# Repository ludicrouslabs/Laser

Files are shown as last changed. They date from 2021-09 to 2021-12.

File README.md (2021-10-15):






## Overview

This all came about due to a need to cut bulk acrylic for some friends and getting sick and tired of loading a CNC router to do it. And I’d be remiss if I didn’t admit this all wouldn’t have happened if a major manufacturer of laser engravers would have simply returned our calls.

With the accessibility of 3D printing and the ability to buy off the shelf components to make almost any machine you can think of, we figured a high-speed engraving laser couldn’t be that hard…. Or could it? Our goal is to make a safe, aesthetically pleasing laser platform that will enable makers to start with mostly 3d printed parts, while giving those who want a more professional system to upgrade to higher quality components. 

Lets see how close this gets.



## Design Status

| Assembly | Progress | Status | Comments | 
|---|:---:|---|---|
| Frame |  | Beta | Build at own risk |
| Panels |  | Beta | Build at own risk |
| X Drive |  | Design | Do not build / Errors expected |
| Y Drive |  | Beta | Build at own risk |
| Z Drive |  | Design | Do not build / Errors expected |
| Z Table |  | Design | Do not build / Errors expected |
| Laser Head |  | Design | Do not build / Errors expected |
| Electrical |  | Design | Do not build / Errors expected |
| Branding |  | Complete | Sticker design complete |

## Documentation

Documentation will become available when the initial design is tested and shown to work as expected.

## Getting Help
discord (https://discord.gg/RAaGxKcNBF)

## Shout Outs

Special thanks to RCF, Steve, Chron, Wile and everyone else for answering the endless stupid questions.

## Licence

All Ludicrous Labs projects are licenced GPL3.

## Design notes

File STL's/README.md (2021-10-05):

# STL's

Please be aware that this project is still in heavy development. None of the STL's should be considered complete or ready for and end user to build. Files posted here are intended for specific testers to download components for reference and review.

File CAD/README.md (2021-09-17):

# CAD

To be uploaded upon completion of initial design.

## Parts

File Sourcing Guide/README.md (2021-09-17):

# Sourcing Guide

Google sheet to be linked at a later date. Much to work on.

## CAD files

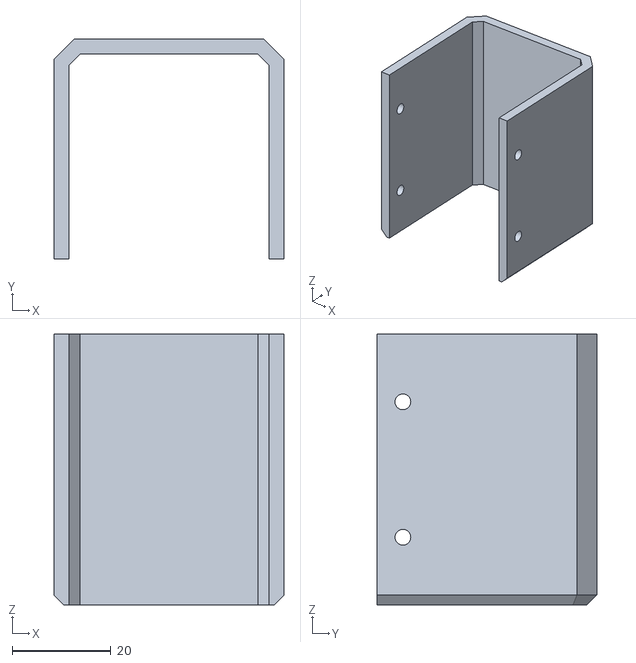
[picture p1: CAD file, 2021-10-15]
STL's/Head/head cover.stl
46.6 x 44.6 x 55.0

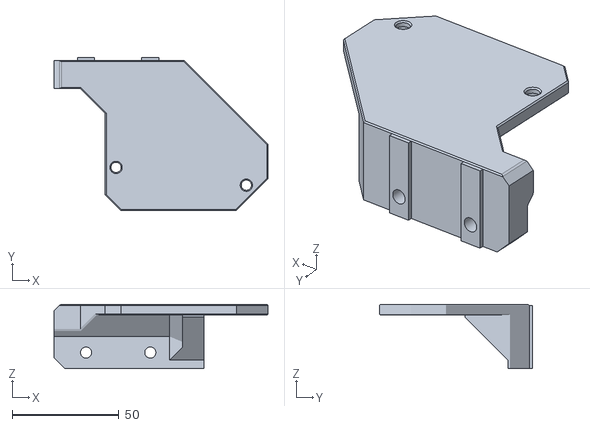
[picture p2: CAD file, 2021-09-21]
STL's/Tools/Test Platform.stl
100.0 x 71.5 x 30.0

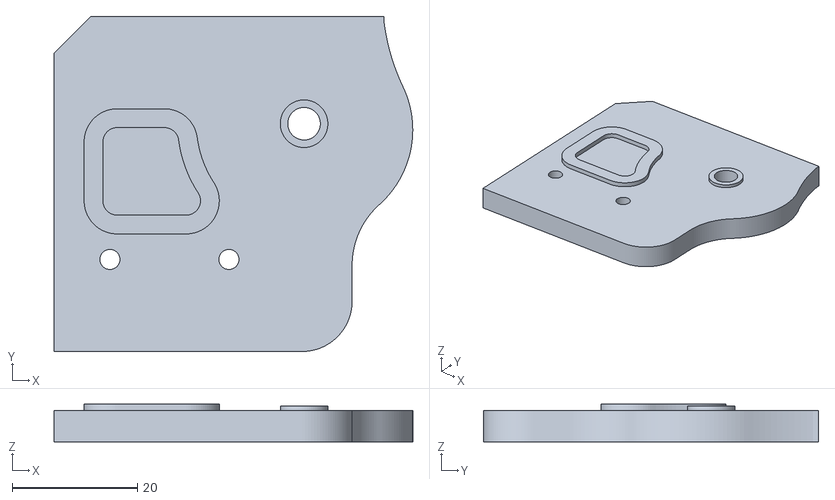
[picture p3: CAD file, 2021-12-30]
STL's/X Drive/X Drive Shim.stl
57.3 x 53.5 x 6.00

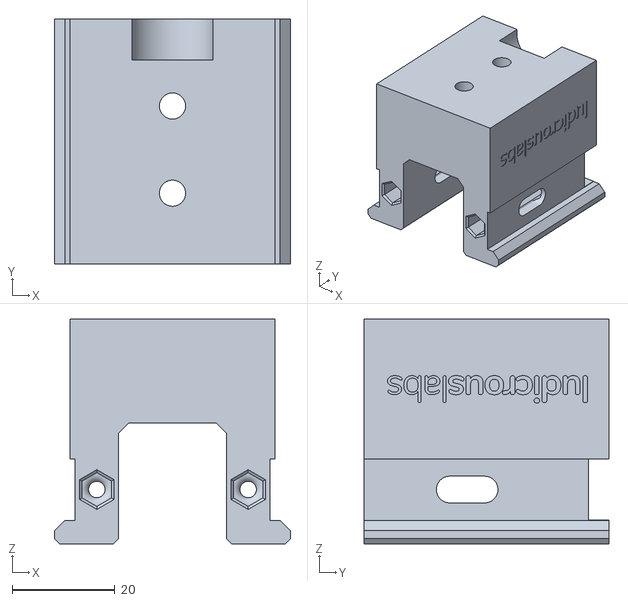
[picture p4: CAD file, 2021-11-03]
STL's/Y Drive/Y Block Top Right.stl
46.0 x 47.8 x 43.8

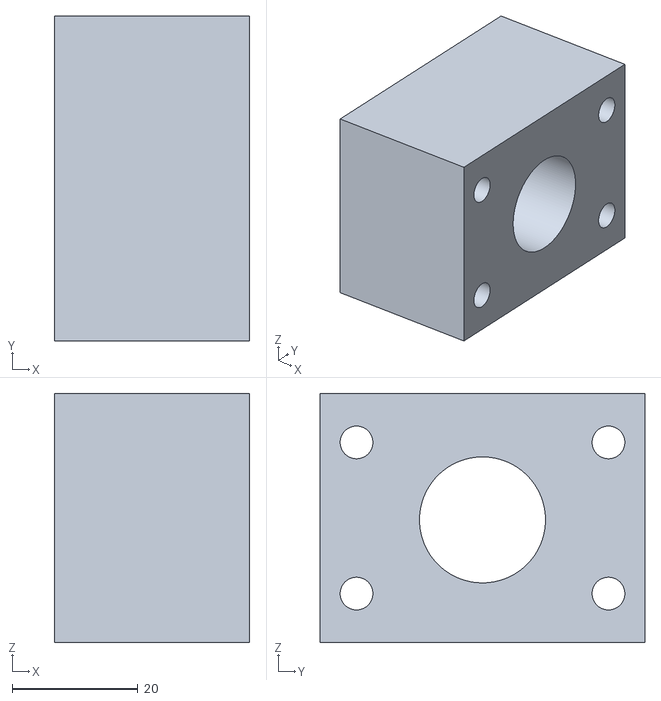
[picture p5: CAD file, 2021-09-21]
STL's/Z Drive/Bed Mount.stl
31.0 x 51.6 x 39.6

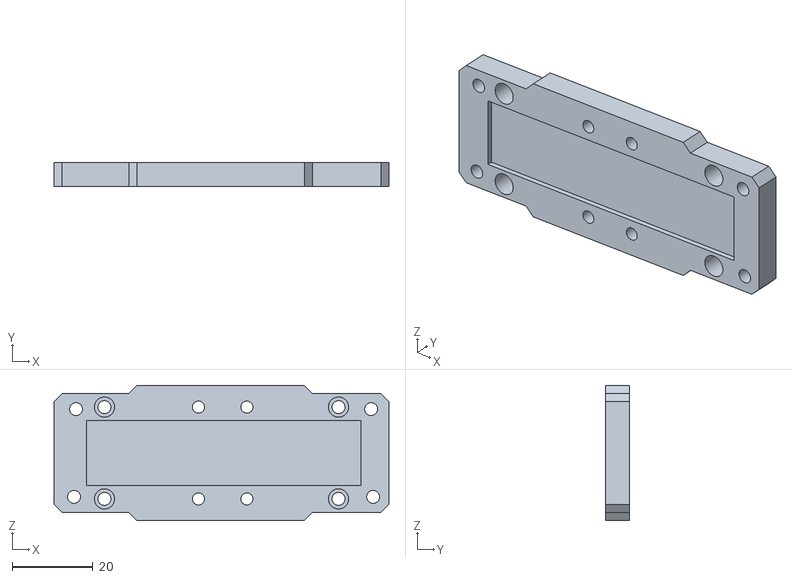
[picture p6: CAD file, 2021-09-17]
STL's/Head/face block.stl
83.0 x 6.00 x 33.5

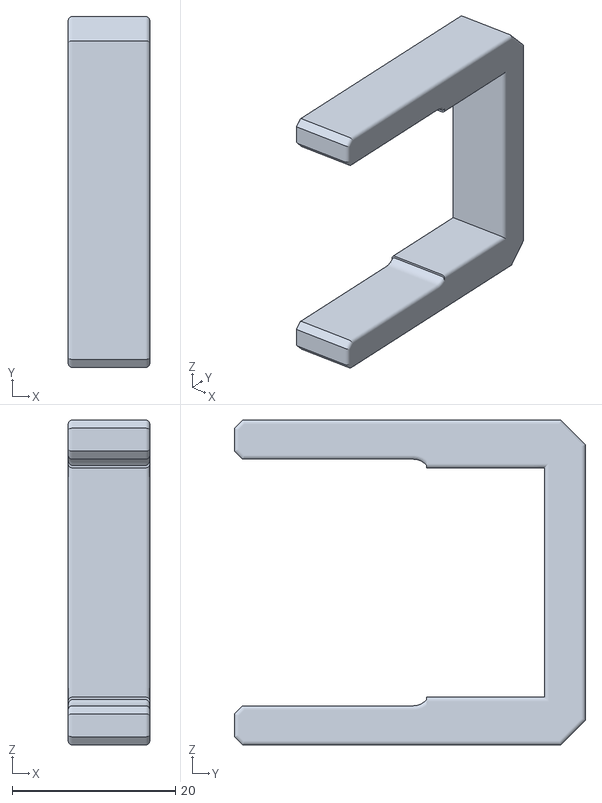
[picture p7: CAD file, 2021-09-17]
STL's/Tools/Alignment Guide.stl
10.0 x 43.0 x 39.8

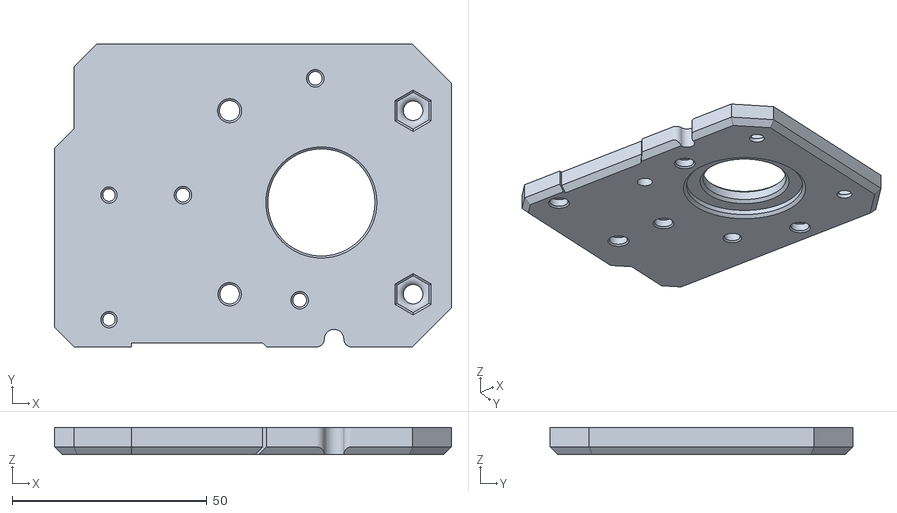
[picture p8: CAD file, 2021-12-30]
STL's/X Drive/X Drive Top.stl
102.0 x 77.8 x 7.00

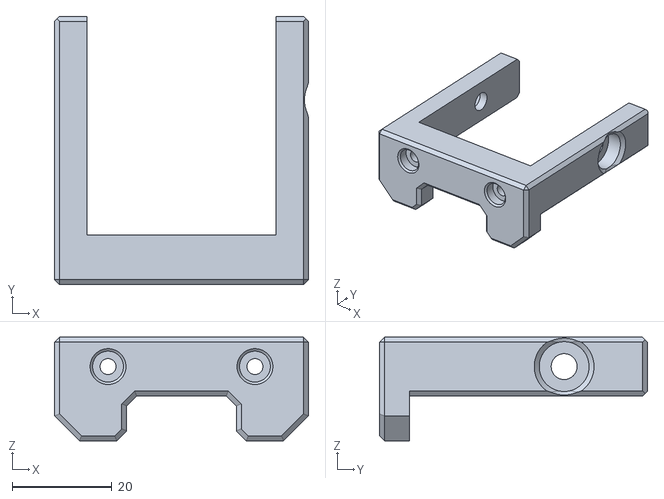
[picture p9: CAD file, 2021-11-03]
STL's/Y Drive/Tension Bracket Right.stl
51.0 x 53.8 x 20.8

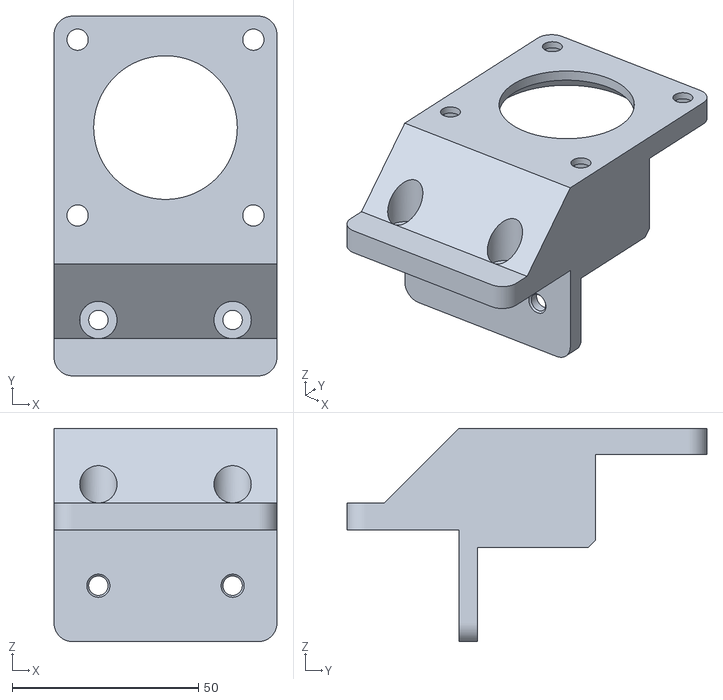
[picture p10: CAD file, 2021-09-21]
STL's/Z Drive/Z Motor Mount Right.stl
59.8 x 96.5 x 57.2

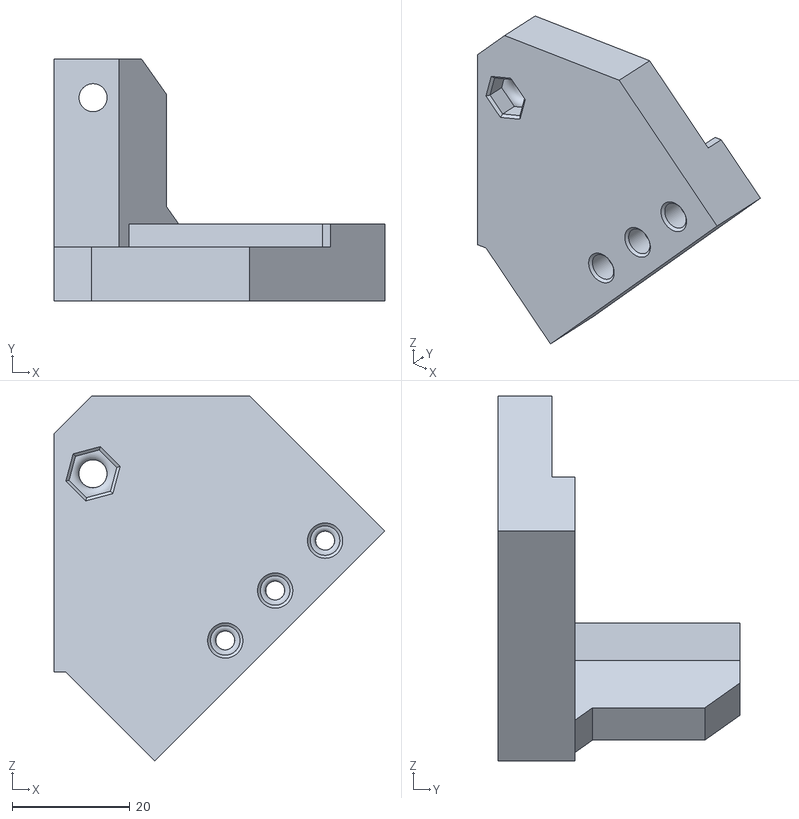
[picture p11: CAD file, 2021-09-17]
STL's/Head/mirror mount.stl
56.2 x 41.2 x 62.0

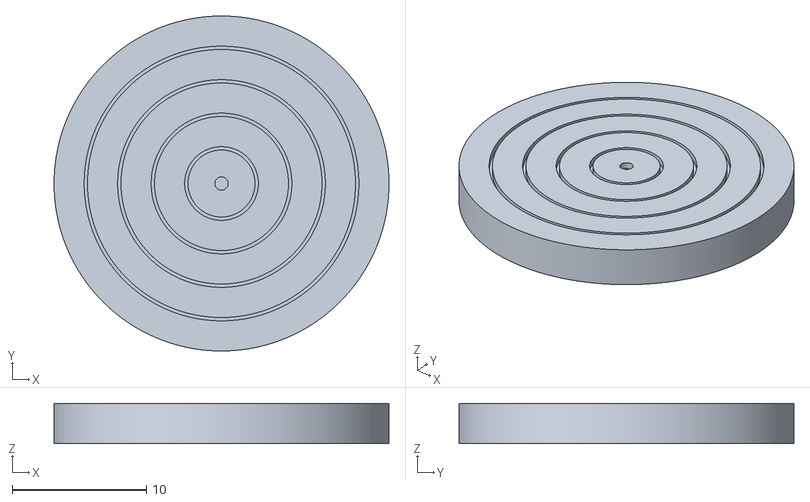
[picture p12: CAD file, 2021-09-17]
STL's/Tools/Target.stl
25.0 x 25.0 x 3.00

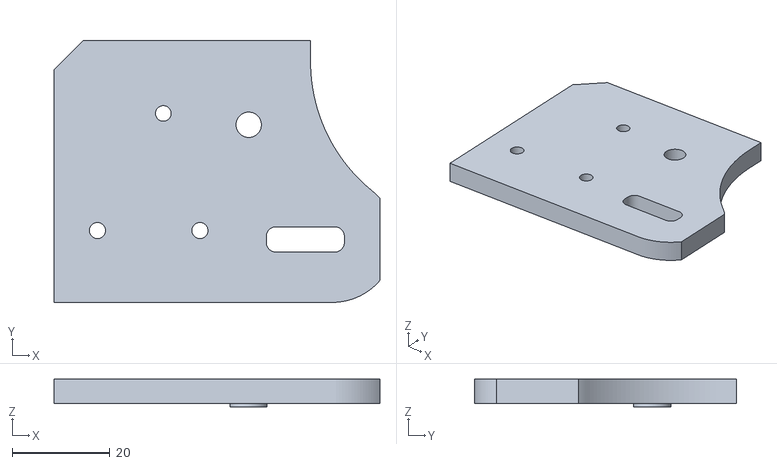
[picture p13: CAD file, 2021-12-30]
STL's/X Drive/X Idler Shim.stl
66.8 x 53.6 x 5.70

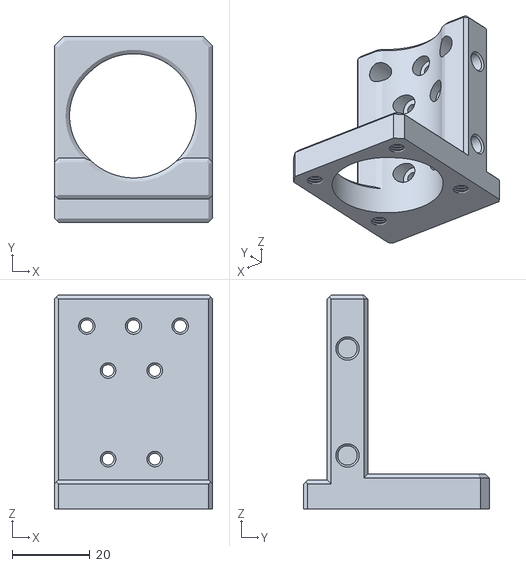
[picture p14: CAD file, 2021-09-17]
STL's/Head/lens mount.stl
40.6 x 47.7 x 55.0

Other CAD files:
STL's/Y Drive/Tension Bracket Left.stl
STL's/Z Drive/Z Motor Mount Left.stl
STL's/X Drive/X Idler Tensioner.stl
STL's/Y Drive/Y Block Top Left.stl
STL's/Head/carriage block.stl
STL's/X Drive/X Drive Bottom.stl
STL's/X Drive/X Drive Cable Cover.stl
STL's/X Drive/X Drive Mid.stl
STL's/X Drive/X Idler Bottom.stl
STL's/X Drive/X Idler Mid.stl
STL's/X Drive/X Idler Top.stl
STL's/X Drive/X Rail Alignment Guide.stl
STL's/Y Drive/Left Motor Drive.stl
STL's/Y Drive/Left Motor Mount.stl
STL's/Y Drive/Right Motor Drive.stl
STL's/Y Drive/Right Motor Mount.stl
STL's/Y Drive/Y Block Bottom x2.stl
STL's/Z Drive/Adapter Plate.stl

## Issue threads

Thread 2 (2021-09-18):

Y Tension Redesign

insurgus, 2021-09-18:
Front tensioners are cracking under load. Require re-design to improve strength.

insurgus, 2021-09-18:
Rev 2 bust. Printing Rev 3.

insurgus, 2021-09-19:
Rev 3 seems to work properly. Good tension.

insurgus, 2021-09-19:
Original

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

New

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

Need to add 45mm M5 or shoulder bolt to bom.

Closed 2021-09-19.

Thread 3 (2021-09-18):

X Motor Torque Insufficent

insurgus, 2021-09-18:
X stepper is skipping at high accelerations. Require different spec for RF support.

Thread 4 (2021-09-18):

X Endstop Design

insurgus, 2021-09-18:
Finish X endstop design and placement.

insurgus, 2021-09-19:
Initial endstop location designed in, but need to check it to see if it's going to be strong enough. Will test print this week and give it a rip. Cable management might be an issue here though.

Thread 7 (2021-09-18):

Magnetic Bed Mount

insurgus, 2021-09-18:
Mag bed with index points.

insurgus, 2021-09-18:
Completed. Added index capability to the plate so that users can fixture projects as desired.

Closed 2021-09-18.

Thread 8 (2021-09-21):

Z Lift Motor Mounts

insurgus, 2021-09-21:
Require design/ testing.

insurgus, 2021-09-22:
Rev 1 seems to work well. Ability to tension properly just by moving the mount and tightening. Likely need to align later but that's a problem for another day.

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

Closed 2021-09-22.

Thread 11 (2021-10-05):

X Motor/Idler Middle Insert

insurgus, 2021-10-05:
Dependencies are top and bottom plates once this is completed. Routing for belts similar to the work that was done for the printer XY motor mounts.

insurgus, 2021-10-05:
Design middle inserts to accommodate belt path routing and provide rigidity to the idler and drive mounts.

insurgus, 2021-10-05:
Insert is complete. Works with existing tension module.

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

Closed 2021-10-05.

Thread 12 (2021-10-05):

Rework X Idler and Drive base plates.

insurgus, 2021-10-05:
Reside and rework to fit middle insert.

Closed 2021-10-06.

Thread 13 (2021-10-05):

Rework X Idler and Drive top plates

insurgus, 2021-10-05:
Reside and rework to fit middle insert.

insurgus, 2021-10-05:
Initial design complete. Needs some special sauce but good enough for testing.

Closed 2021-10-06.

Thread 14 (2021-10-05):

X Drive Motor Mounting

insurgus, 2021-10-05:
Rework the motor mount to clean things up.

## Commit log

2021-09-17 initial up
    [Left Motor Drive.stl, Left Motor Mount.stl, Right Motor Drive.stl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]
2021-09-17 adding z adapter plates
    [Adapter Plate.stl]
2021-09-17 Idler update
    [Tension Bracket Left.stl, Tension Bracket Right.stl, Y Block Top x2.stl]
2021-09-17 adding tools
    [Alignment Guide.stl, Target.stl]
2021-09-18 bed mount draft
    [Bed Mount.stl]
2021-09-18 tension and bed mount rev2
    [Bed Mount.stl, Tension Bracket Left.stl, Tension Bracket Right.stl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]
2021-09-18 chamfer print face
    [Y Block Top x2.stl]
2021-09-18 magnetic bed mount
    [Bed Clip.stl, Bed Mount.stl]
2021-09-21 clearance updates + tool
    [Bed Clip.stl, Bed Mount.stl, Test Platform.stl]
2021-09-21 initial z mount
    [Z Motor Mount Left.stl, Z Motor Mount Right.stl]
2021-09-21 Update bolt clearance
    [Z Motor Mount Left.stl, Z Motor Mount Right.stl]
2021-09-21 Clearance changes
    [Right Motor Mount.stl]
2021-09-21 Cleanup
    Not compatible with new design. Require rework.
    [Bed Clip.stl, Bed Mount.stl]
2021-10-05 Redesign Mid Insert
    reworked to reduce plastic required in printing. Initial top and bottom uploaded for testing.
    [X Idler Bottom.stl, X Idler Mid Insert.stl, X Idler Top.stl]
2021-10-06 Rework X Drive
    Rework of X drive components. Easier to assemble, less plastic and cleaner design.
    [X Drive Bottom.stl, X Drive Mid.stl, X Drive Shim.stl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]
2021-10-14 Add wiring path
    Wiring path for X endstop and stepper motor. Prep complete for cable chain mounts.
    [X Drive Bottom.stl, X Drive Cable Cover.stl, X Drive Mid.stl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]
2021-10-14 Update for X Endstop
    Arm to hit X Endstop
2021-10-15 Addition of REMOVE text
    Addition of REMOVE text to aid in assembly.
    [X Idler Bottom.stl]
2021-10-15 Optional Part
    Optional head cover for those that want it.
    [head cover.stl]
2021-10-15 Branding Update
    Test branding for beta release
    [Left Motor Drive.stl, Right Motor Drive.stl, Y Block Top Left.stl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]
2021-11-03 Fastener Clerance
    Fixes for fasteners heads. Little too tight given printing orientation.
    [Tension Bracket Left.stl, Tension Bracket Right.stl, Y Block Top Right.stl]
2021-11-03 Shoulder Bolt Clerance
    increasing side of shoulder bolt head slots for clearance.
    [X Idler Tensioner.stl, X Idler Top.stl]
2021-11-03 Update Shim
    Shim update
    [X Idler Shim.stl]
2021-12-28 Fitment Tweaks
    Changing some sizing and re-locating fasteners for better fitment.
    [X Drive Bottom.stl, X Drive Mid.stl, X Drive Top.stl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]
2021-12-30 Clearance
    Clearance for M3 fasteners.
    [X Drive Shim.stl, X Drive Top.stl, X Idler Shim.stl]
